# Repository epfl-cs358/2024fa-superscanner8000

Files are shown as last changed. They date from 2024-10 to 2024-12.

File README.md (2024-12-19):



# Superscanner8000
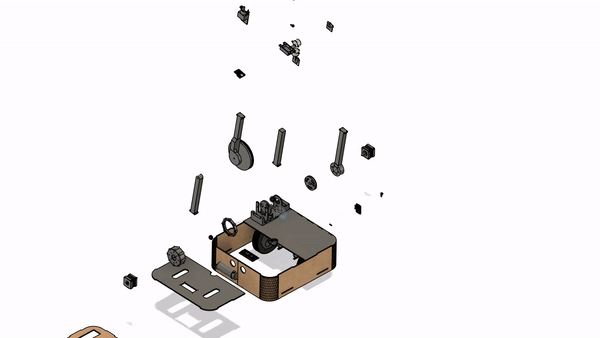
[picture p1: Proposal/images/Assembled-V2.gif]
CAD of the assembled Superrrrscanner

## Authors
   - [Noa Emien Ette](https://github.com/Noaemien)
   - [Kevan Lam Hopyang](https://github.com/KevanLam)
   - [Louis Léonard Marie Larcher](https://github.com/loulou413)
   - [Antoine Baptiste Gauthier](https://github.com/gautierantoine195)
   - [Mateo Tiedra](https://github.com/mateotiedra)
   - [Ugo Novello](https://github.com/Laggrif)

<details>
  <summary>Table of Contents</summary>
  <ol>
    <li>
      <a href="#about-the-project">About The Project</a>
      <ul>
        <li><a href="#authors">Authors</a></li>
        <li><a href="#project-description">Project Description</a></li>
        <li><a href="#project-structure">Project Structure</a></li>
      </ul>
    </li>
    <li>
      <a href="#make-your-own-superscanner8000">Make Your Own SuperScanner8000</a>
      <ul>
        <li><a href="#built-with">Built With</a></li>
        <li><a href="#prerequisites">Prerequisites</a></li>
        <li><a href="#hardware-assembly">Hardware Assembly</a></li>
        <ul>
          <li><a href="#main-body">Main Body</a></li>
          <li><a href="#arm">Arm</a></li>
          <li><a href="#gearbox">Gearbox</a></li>
          <li><a href="#motor-housings">Motor Housings</a></li>
          <li><a href="#assembly-of-the-arm">Assembly Of The Arm</a></li>
        </ul>
        <li><a href="#electronic">Electronic</a></li>
        <ul>
          <li><a href="#diagram">Diagram</a></li>
        </ul>
        <li><a href="#software">Software</a></li>
      </ul>
    </li>
    <li><a href="#gratitude-and-appreciation">Gratitude and Appreciation</a></li>
  </ol>
</details>

## Project Description 

The core of this project idea is to make a mobile robot capable of identifying the object of interest and taking pictures of it from all (possible) angles. This would be paired with a desktop application that would receive the images and apply the user-selected 3D reconstruction algorithm.

From this description, we can identify several key components the project needs:

1. **The Robot**:
   - 1.1: Navigate and plan routes around the object.
   - 1.2: Segment view and recognize the object of interest.
   - 1.3: Translate camera on the Z-axis whilst tracking the object of interest.

2. **The Desktop Application**:
   - 2.1: User can choose the object of interest.
   - 2.2: Process images sent by the robot using 3D reconstruction algorithms (NeRF, 2DGS, Multi-view stereo).

Nowadays, one does not need specialized high-end equipment to 3D scan objects. Most of us already have the necessary equipment—a smartphone, as long as it has a functioning camera and adequate software. For this project, we will not be using a smartphone, as having an integrated camera gives the robot higher usefulness without drastically increasing complexity.

In order to move the camera, we will use an arm with two segments, each powered by a stepper motor (like the Pixar lamp), fixed on top of the robot and oriented perpendicular to the wheels. In addition, the camera will be fixed to the arm using two servos offering roll and pitch control.

Most currently existing 3D object scanners are catered to small objects, rotating the object and photographing it from a fixed camera. We decided to take a different approach with the goal of providing more flexibility while keeping the complexity as low as possible.

<p align="right">(<a href="#readme-top">back to top</a>)</p>

## Project Structure

Below is a brief explanation of this repository's structure to provide context and aid readers' comprehension in the following sections of this document.
- `code` directory: contains all the code for the different parts of the project.
    - `hardware`: directory: contains all the code related to the hardware (motor movement, camera setup, connection to webserver) 
    - `software`: directory: contains all the code related to the software (webapp, navigation, reconstruction of 3d model...)
- `design` directory: contains all the 3D modeling files and exports along with the laser cut sheets.
- `diagrams` directory: contains all diagrams relate to the project
- `documentation` directory: contains all the pictures and schematics to be able to reproduce this project.
- `proposal` directory: the original document used to write the initial project proposal.

<p align="right">(<a href="#readme-top">back to top</a>)</p>

## Make your own SuperScanner8000

This section is dedicated to explaining how to build this project yourself! (All the printing/cutting part are available)

### Built with

   * [][Python-url]
   * [][Cpp-url]

### Prerequisites
Comprehensive list of elements we used in our project along with needed equipment. To construct the device, one should

Buy:

- 2 Esp-32 Cam + ov5640 (for the camera on top => better image resolution, if you got a better camera, use it)
- Lot of PETG
- 2 NEMA-17 (stepper motor) (17HS4401 + A4988)
- 2 Chihai CHF-GM37-550ABHL (brush motor) + L298N (driver)
- 2 28BYJ-48 StepperMotor (stepper motor) + ULN2003 (driver)
- QAPass 1602a

Have access to:

- LIPO Batterie
- LIPO box (you can make it your own : [LIPO Protection tuto](https://github.com/epfl-cs358/cs358-resources/tree/main/cad/lipo_protection))
- Batterie management system (3S 12V 40A Lithium Batterie BMS)
- 3D printer with TPU filament (for the outer wheel)
- 3D printer with PET filament (bunch of it, pla should make it right too)
- Laser cutting machine
- MDF board 4mm
- Airsoft Bullets (gearbox)
- 6 small ball bearings (gearbox)
- 4 small omni bearings (caster wheel)
- Ball (caster wheel : e.g. table football ball)
- 4 Magnets (QAPass)
- Belt (Arm)
- 6mm Stailness Steel bar (Arm)
- 3 mm and 2.5 mm Screws
- Driller
- Bunch of different screwdrivers
- Soldering kit

<p align="right">(<a href="#readme-top">back to top</a>)</p>

### Hardware Assembly

##### Main Body

###### Base

Laser cut the following MDF (4mm) files :
   - [Bottom Base](design/dxf/bottom_base.dxf)
   - [Side Base](design/dxf/side_full.dxf)
   - [Top Base Front](design/dxf/top_base_front.dxf)
   - [Top Base Back](design/dxf/top_base_back.dxf)
   - 3 * [Calibrate 1](design/dxf/calibrate1)
   - 3 * [Calibrate 2](design/dxf/calibrate2)

3d Print the following folder :
   - [Components Support](design/prints/components_supports)

The side is made to be foldable to give our SuperScanner8000 round corners. Be careful with these specific parts as they could break. 
You can assemble the bottom and side by glueing them but we recommend glueing the top parts once you have all the electronics setup inside.

###### Wheels

3D print the following parts : 
   - 2 * [Inner Wheel](design/prints/inner_wheel.stl)
   - 2 * [Outer Wheel](design/prints/outer_wheel.stl) (Beware you need to print this in TPU)

###### Caster Wheel

3D print the following folder : 
   - [Caster Wheel Folder](design/prints/caster)

You will also need the 4 omni bearings for this part.

###### Structures for electronics

3D print the following parts :
   - [CNC Shield Support](design/prints/CNC_shield_support.stl)
   - [ESP32-S2 Support](design/prints/ESP32-S2_support.stl)
   - [LiPo Support](design/prints/LiPo_support.stl)
   - [Chihai Support](design/prints/chihai_supports.stl)
   - [LiPo Bottom](design/prints/lipo_box/Lipo_bottom.stl)
   - [LiPo Box](design/prints/lipo_box/Lipo_box.stl)

Here, drill your own hole to make your own wire management.

##### Arm

###### Arm

3D print the parts in these folders :
   - [Arm Folder](design/prints/long_arm)
   - [Top Axle Folder](design/prints/top_axle)

3d print this part to hold the belt together :
   - [Belt Holder](design/prints/belt_holder.stl)

You should print 2 times esp_case2 for the cam in the box that we use for object detection. You will need the 6mm stainless steel bar for the elbow connection of the arm.
We opted to glue our belt into one piece instead of the belt holder in the end but both solutions are fine.

###### Gearbox

3D print the parts in the actuator folder :
   - [15th Planet Carrier](design/prints/actuators/15th_planet_carrier.stl)
   - [15th Sun](design/prints/actuators/15th_sun_stage1.stl)
   - 3 * [25th Planet Stage 1](design/prints/actuators/25th_planet_stage1.stl)
   - 3 * [25th Planet Stage 2](design/prints/actuators/25th_planet_stage2.stl)
   - [Motor Base Ring](design/prints/actuators/Nema17_base_ring.stl)
   - [Motor Clamp](design/prints/actuators/Nema17_clamp.stl)
   - [Motor Mount](design/prints/actuators/nema17_mount.stl)

You'll also need the 6 ball bearings and the airsoft bullets to create this gearbox.
We followed [this tutorial](https://www.thingiverse.com/thing:4428749/) to create our gearbox.

###### Motor Housings

3D print the following parts :
   - [Nema17 Housings](design/prints/housing_on_base.stl)

Here we also used some small carpet textile to reduce the stepper motor noise.

<p align="right">(<a href="#readme-top">back to top</a>)</p>

###### Assembly Of The Arm

Once you have printed all these components you will firstly you'll want to screw the 4 arm parts together as well as the upper arm (make sure you add the metal/stainless steel bar at the elbow and the camera in the upper arm section). You can also screw the housings to the top of the base and screw the gearbox to a stepper motor in parallel. Now you can screw the arm to the gearbox and finally place the stepper motors in the housings (first thebelt one and then the gearbox one, don't forget the carpet). Add the belt and you'll be good to go!

### Electronic
#### Diagram
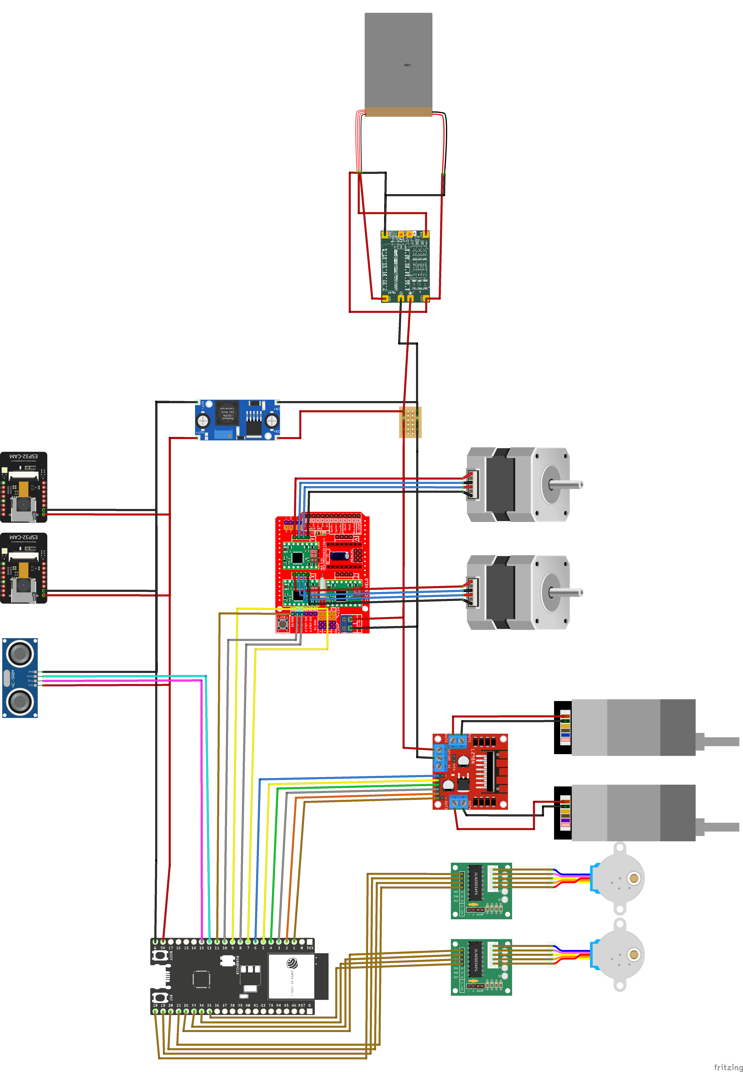
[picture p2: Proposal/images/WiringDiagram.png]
elctronic diagram


### Software
The structure of the software as well as an installation guide can be found in the [software directory](code/software).

## Possible Improvements

Here are a few improvements we thought of for this project.

### Hardware

A non-exhaustive list :
   - A better LiPo battery : ours is starting to die out and can't power the LEDs at full capacity.
   - Different / more precise motors for the wheels : our robot has slight trouble going perfectly straight.
   - A third stepper for the camera to avoid inverse kinematics.
   - Screw the elbow instead of using a stainless steel bar : would need the perfect screw that is partialy threaded so it can rotate around the other arm.
   - Metal balls for the gearbox : our airsoft balls start to melt and decompose.
   - A better design for the nema 17 housings to make sure the gear box doesn't bend due to the pull of the belt

## Gratitude and Appreciation
We would like to express our special thanks to our assisstant [Pinar](https://github.com/pinar-oray) and [Julian](https://github.com/julianmarmier), whose insights and suggestions were instrumental in shaping our super scanner. We are also grateful to [Timofey](https://github.com/kreslotim) for his technical support and encouragement and constructive feedback.

And I (Kevan) would like to thanks my peers, my friends for this fun project.

[Python.org]: https://img.shields.io/badge/Python-brightgreeen?style=flat&logo=python&logoColor=FFE873&color=306998
[Python-url]: https://www.python.org/
[Cpp.org]: https://img.shields.io/badge/C%2B%2B-blue?logo=cplusplus
[Cpp-url]: https://isocpp.org/

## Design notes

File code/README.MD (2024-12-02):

## Superscanner 8000's general structure
#### Codesource's structure
The project consists of two main directory: the software and the hardware. In the hardware directory there is all the code running in the arduino board directly attached to the robot. The software sends instructions to the hardware, and the hardware gather and share informations back to the software. In the software directory there is all the code running on the computer.

## Robot movements
The first part of the system make the robot move to the right positions around the object. To scan it as precisely as possible. In order to do that the computer and the robot are both connected to a WiFi network and the robot host a webserver on which the computer can send requests

#### Movement API
- `POST /move`: Instructs the robot to move forward. **Parameters:**
    - `direction` (string): The direction of rotation, either `forward` or `backward`.
    - `distance` (integer): The distance for which the robot should move. If it is not specified, the robot move until instructed otherwise.
- `POST /stop`: Instructs the robot to stop all movement. No parameters.
- `POST /rotate`: Instructs the robot to rotate by a specified angle. **Parameters:**
    - `direction` (string): The direction of rotation, either `left` or `right`.
    - `angle` (integer): The angle in degrees by which the robot should rotate. If it is not specified, the robot rotate until instructed otherwise.
- `POST /arm`: Instructs the robot to rotate by a specified angle. **Parameters:**
    - `hips` (integer) [0,180]: The angle in degrees between the base plan and the first segment of the arm.
    - `knee` (integer) [-180,180]: The angle difference in degrees between the first and second segment
    - `ankle` (integer) [0,360]: The angle difference in degrees between the camera to the top and the second segment

## Computing the 3D model
The robot sends the pictures it takes to the computer in order to run AI model on computer and compute the 3D model.

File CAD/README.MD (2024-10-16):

# CAD designs imported from Fusion360 team folder

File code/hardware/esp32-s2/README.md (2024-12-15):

# ESP32 API

## Overview
The API can be accessed from the `SPOT-iot` Wifi using the adress [`http://superscanner8000/`](http://superscanner8000/). The file `code/esp32-s2/esp32s2.py` makes the API available through an `ESP32S2` class for easy usage in python code.

## Endpoints

> ### GET `/status`
> return format:
> <pre><code>    {
>         "direction": one of <i>forward</i>, <i>backward</i>, <i>left</i>, <i>right</i>, <i>hard left</i>, <i>hard right</i>, <i>stop</i> 
>     }
> </code></pre>
> Returns the current movement the scanner is performing.

> ### POST `/fwd`
>    body format:
>
>        {
>            "ms": value
>        }
> 
> Makes the scanner run forward for `ms` milliseconds. If `ms <= 0` runs forever.

> ### POST `/bwd`
>    body format:
>
>        {
>            "ms": value
>        }
> 
> Makes the scanner run backward for `ms` milliseconds. If `ms <= 0` runs forever.

> ### POST `/lft`
>    body format:
>
>        {
>            "ms": value
>        }
> 
> Makes the scanner turn left for `ms` milliseconds. If `ms <= 0` runs forever.

> ### POST `/rgt`
>    body format:
>
>        {
>            "ms": value
>        }
> 
> Makes the scanner turn right for `ms` milliseconds. If `ms <= 0` runs forever.

> ### POST `/hlft`
>    body format:
>
>        {
>            "ms": value
>        }
> 
> Makes the scanner turn on itself anti-clockwise for `ms` milliseconds. If `ms <= 0` runs forever.

> ### POST `/hrgt`
>    body format:
>
>        {
>            "ms": value
>        }
> 
> Makes the scanner turn on itsels clockwise for `ms` milliseconds. If `ms <= 0` runs forever.

> ### POST `/stp`
>    
> Makes the scanner stop as quickly as possible. Does not need any body.

> ### GET `/arm/status`
>    return format:
>
>        {
>            "x": x position where the arm is
>            "y": y position where the arm is
>            "q1": angle of first stepper in degrees
>            "q2": angle of the second stepper in degrees
>            "moving": boolean indicating whether the arm is moving or not
>        }
> 
> Returns informations about the arm.

> ### POST `/arm/goto`
>    body format:
>
>        {
>            "x": target x position
>            "y": target y position
>            "angles": boolean indicationg whether x and y are positions or angles
>        }
> 
> Makes the arm move to the given position
>> might return error code `422` if coordinates or angles are not valid

> ### POST `/arm/stop`
> 
> Stops the arm as quickly as possible. Does not need any body

> ### GET `/cam/status`
>    return format:
>
>        {
>            "alpha": alpha angle where the cam wants to go
>            "beta": beta angle where the cam wants to go
>            "moving": boolean indicating whether the camera is moving or not
>        }
> 
> Returns informations about the camera.

> ### POST `/cam/goto`
>    body format:
>
>        {
>            "alpha": target angle for vertical movement
>            "betha": target angle for horizontal movement
>        }
> 
> Makes the camera move to the given angles
>> Might return error code `422` if angles are not valid

> ### POST `/cam/stop`
> 
> Stops the camera as quickly as possible. Does not need any body

## class `ESP32S2`

Interfaces with the API to provide an abstracted access to the scanner.

> ### `ESP32S2()`
> Class constructor. Does not require any parameters.

> ### `forward(self, time)`
> - `time`: duration of movement in ms. Moves infinitely if <= 0
> - returns: `0` if operation was successful, `-1` otherwise

> ### `backward(self, time)`
> - `time`: duration of movement in ms. Moves infinitely if <= 0
> - returns: `0` if operation was successful, `-1` otherwise

> ### `left(self, time)`
> - `time`: duration of movement in ms. Moves infinitely if <= 0
> - returns: `0` if operation was successful, `-1` otherwise

> ### `right(self, time)`
> - `time`: duration of movement in ms. Moves infinitely if <= 0
> - returns: `0` if operation was successful, `-1` otherwise

> ### `hard_left(self, time)`
> - `time`: duration of movement in ms. Moves infinitely if <= 0
> - returns: `0` if operation was successful, `-1` otherwise

> ### `hard_right(self, time)`
> - `time`: duration of movement in ms. Moves infinitely if <= 0
> - returns: `0` if operation was successful, `-1` otherwise

> ### `stop(self)`
> - returns: `0` if operation was successful, `-1` otherwise

> ### `direction(self)`
> - returns: a `string` giving the current direction or `None` if request was unsuccessful

> ### `arm.goto(self, x_coord, y_coord)`
> - `x_coord`: target x coordinate in cm
> - `y_coord`: target y coordinate in cm
> - returns: `0` if operation was successful, `-1` otherwise

> ### `arm.stop(self)`
> - returns: `0` if operation was successful, `-1` otherwise

> ### `arm.pos(self)`
> - returns: `(x, y)` tuple representing the target coordinated of the arm or `None` if the request was unsuccessful

> ### `arm.is_moving(self)`
> - returns: a `boolean` indicating whether the arm is moving or `None` if the request was unsuccessful

## `__main__` in `esp32s2.py`

Running `esp32s2.py` provides a small graphical interface to test movements without having to write code.

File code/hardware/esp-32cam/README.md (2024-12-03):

Run the Esp32-cam.ino on the esp and then run the socket receiver.py The python script will send the computer's IP and the Esp will use this ip to create an udp connection and send the frames it captures.

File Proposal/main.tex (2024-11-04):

\documentclass{article}
\usepackage[utf8]{inputenc}
\usepackage{textcomp}
\usepackage{gensymb}
\usepackage{geometry}
\usepackage{fancyhdr}
\usepackage{tkz-euclide}
\usepackage{ragged2e}
\usepackage{hyperref}
\usepackage{float}
\usepackage{tikz}
\usepackage{float}
\usepackage{multirow}
\usepackage{biblatex}
\usepackage[graphicx]{realboxes}
\addbibresource{refs.bib}

\pagestyle{fancy}
\geometry{top=3cm, bottom=2.5cm, left=3.5cm, right=3.5cm}
\rhead{CS-358}
\lhead{\leftmark}
\fancyfoot[R]{\leftmark}
\fancyfoot[C]{}
\fancyfoot[L]{Page \thepage}
\renewcommand{\footrulewidth}{1pt}
\usepackage{multicol}
\title{CS-358: Individual Project Proposal}
\author{Noa Ette - 363760\\Mateo Tiedra - 356525\\Kevan Lam - 356395\\Louis Larcher - 361002\\Ugo Novello - 329763\\Antoine Gautier - 356442}
\date{\today}

\begin{document}

\maketitle
\vspace{45mm}
\tableofcontents
\newpage
\section{Project Description: Autonomous 3d Object Scanner}

The core of this project idea is to make a mobile robot capable of identifying the object of interest and taking pictures of it from all (possible) angles. 
This would be paired with a desktop application that would receive the images and apply the user selected 3d reconstruction algorithm.\\

From this description we can identify several key components the project needs: \begin{enumerate}
    \item \texttt{The Robot}:
    \begin{description}
            \item[1.1] Navigate and plan routes around object.
            \item[1.2] Segment view and recognize object of interest.
            \item[1.3] Translate camera on z axis whilst tracking object of interest.
    \end{description}
    \item \texttt{The Desktop Application}:
    \begin{description}
        \item[2.1] User can choose object of interest.
        \item[2.2] Process images sent by robot using 3d reconstruction algorithms (NeRF \cite{mildenhall2020nerf}, 2DGS \cite{Huang2DGS2024}, Multi-view stereo)
    \end{description}
\end{enumerate}

Nowadays, one does not need specialised high end equipment in order to 3d scan objects. Most of us already have the sufficient equipment needed, a smartphone, given that it has a functioning camera and the adequate software. \\
For this project we will not be using a smartphone as it gives the robot higher usefulness and does not drastically increase complexity to have an integrated camera. 

In order to move the camera we will use an arm with two segments each powered by a stepper motor (like the Pixar lamp) fixed on top of the robot and oriented perpendicular to the wheels. In addition, the camera will be fixed to the arm using two servos offering roll and pitch control.

Most currently existing 3d Object scanners are catered to small objects \cite{desktop3dscanner}, rotating the object and photographing it from a fixed camera. We decided to take a different approach with the goal to give more flexibility while keeping the complexity as low as possible.

\newpage
\section{Related Projects}
We have looked at various related projects whilst trying to figure out how to design ours in the best possible manner.

We figured a mostly square base with two motors placed on diagonal wheels would be the most practical while being resource efficient and simple. This setup allows the "car" part of the robot to spin on itself, removing the need of having the arm holding the camera spin. This kind of movement is principally inspired by tanks, excavators and other tracked vehicles, except the two wheels on each side are independent instead of linked by a track.

The arm on the other hand takes inspiration from the many existing robotic or industrial arms existing. More particularly, we found this design \cite{cameraArm} which achieves a similar purpose as ours. Moving the motor for the second joint to the base is a key element of the design since it allows to have weaker motors and an overall lower center of gravity.

Unfortunately we have been unsuccessful in finding a project where a robot tracks an object, rotating around it. This poses a particular computer vision challenge as the robot needs to be able to recognise the object from completely distinct angles. Thanks to the fact that the robot will be navigating using video from an ESP32-CAM on the front of the robot, basic object tracking like those in opencv will most likely be sufficient.

\section{User Stories}

The final product of this project is something that could be useful to many people from different horizons. \\
In one case, one could imagine a real estate agent, wanting to provide virtual visits of a home he is selling. Instead of having to contact a freelance 3D artist to remodel the home, probably costing thousands, they would be able to simply 3d scan the area using the robot and software made in this project, saving plenty of time and money. Some companies have already ventured into real-estate specific 3d scanning \cite{matterport}. \\
Another imaginable use case is for professional 3d artists wanting to use realistic large objects in their 3d scenes. The conventional way to scan these objects would be to manually take pictures of them. Something that is very time consuming and sometimes requires particular gymnastics skills.
I personally have a little bit of experience with manually 3d scanning objects and can personally attest that, depending on the object, it can take a frustratingly long amount of time.

It could be an interesting demonstration for the EPFL Open House as it demonstrates the link between 3d art and computer science by leveraging an intelligent robot to optimise the workload of different career paths.

\section{Long term view}

Given a long term viewpoint, we could easily imagine different form factors being based on this project being developed for many different use cases. 

At a much larger scale, terrestrial and aerial 3d scanning robots could be used to map entire city's. Re-creating what would take thousands if not millions of man hours. This data could be used to train autonomous vehicles on real city's though simulation or for many other projects.

At a smaller scale, this technology could be redesigned on an aquatic form factor in order to map ocean floors and areas inaccessible by humans.

\newpage
\section{Physical description}

The robot takes the form of a square "car" with four wheels, 2 of which are powered by brushed motors. An ESP-32 cam on the front of the car allows to make decisions on the movement of the car regarding it environment, this will be further detailed in the next section. On top of the car lies an arm with two joints, each powered by a stepper motor. The arm is facing perpendicular to the direction of travel and on top of it is mounted a second esp-32 cam with an upgraded OV5640 camera. This camera contributes to the navigation but most importantly takes pictures of the object of interest from different angles and at different heights for later reconstruction. The camera is fixed to the arm using two servos, one controlling the pitch and the other the roll.

Regarding the control of all these motors, both esp-32 cam being quite limited in terms of I/O, we have a third micro-controller to handle them.

In terms of power, our thing will work on LiPo batteries, with a battery management board and voltage converters ensuring adequate power to all parts.

See images in the next page for a visual representation of the robot.

\newpage

\begin{figure}[H]
    \centering
    \begin{minipage}{0.45\textwidth}
        \centering
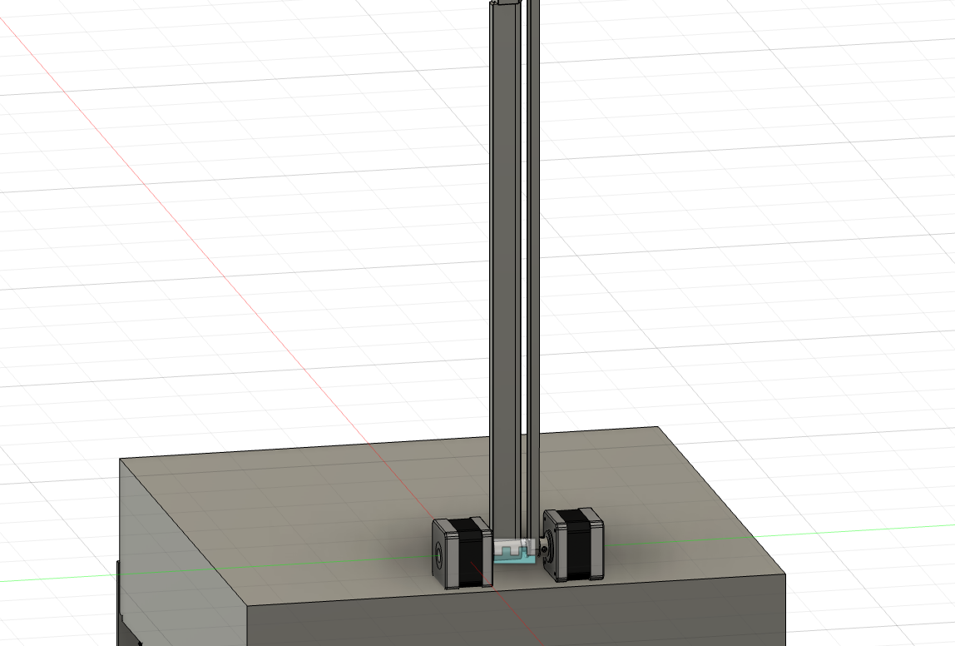
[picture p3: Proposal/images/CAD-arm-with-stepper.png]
        
        \caption{Arm with stepper motors}
        \label{fig:image1}
    \end{minipage}
    \hfill
    \begin{minipage}{0.45\textwidth}
        \centering
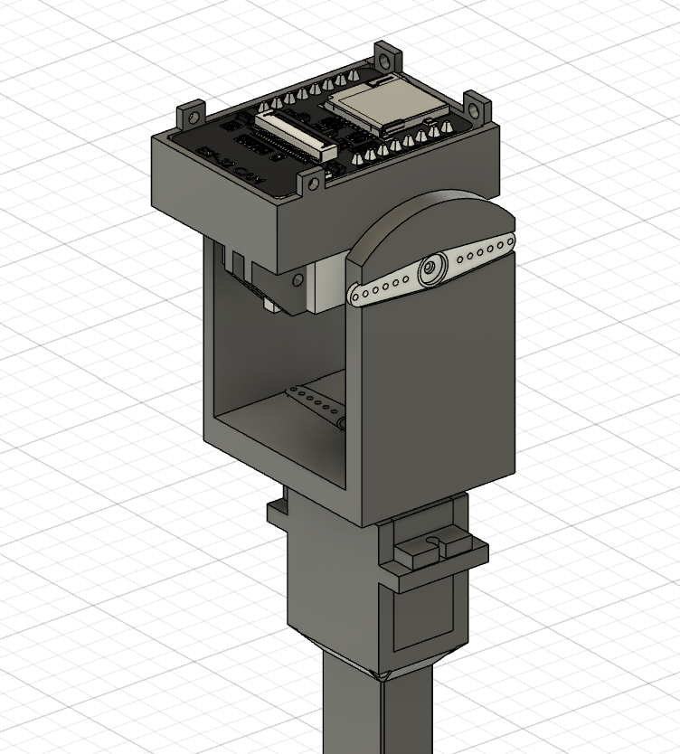
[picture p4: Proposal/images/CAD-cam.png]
        
        \caption{Head of the arm with camera}
        \label{fig:image2}
    \end{minipage}
    \label{fig:sidebyside}
\end{figure}

\begin{figure}[H]
    \centering
    \begin{minipage}{0.45\textwidth}
        \centering
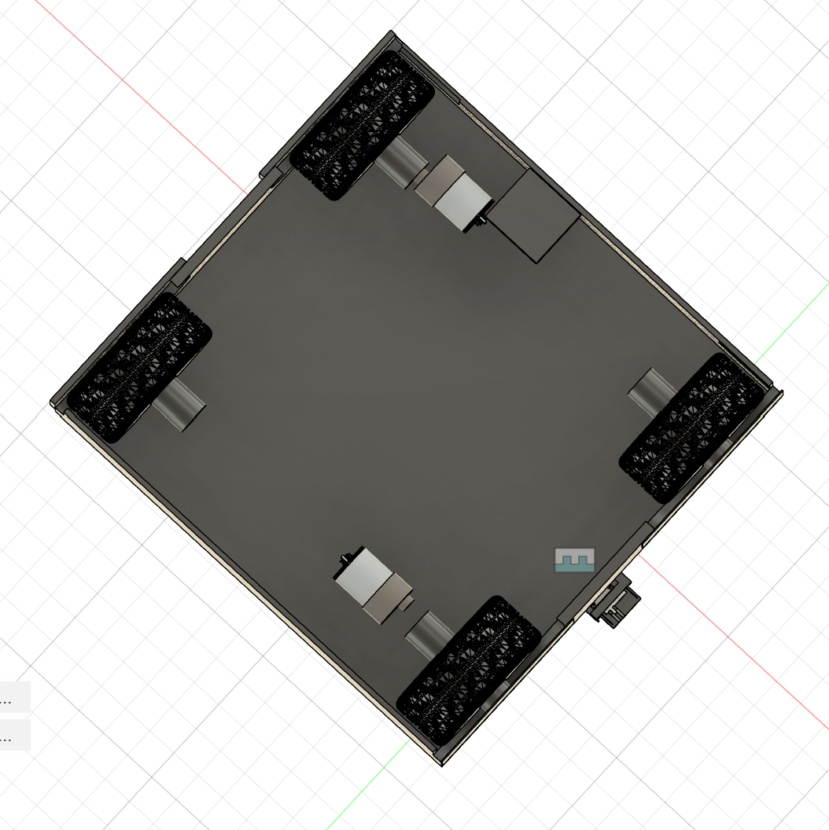
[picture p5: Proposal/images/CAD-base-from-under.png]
        
        \caption{Base and wheels from underneath}
        \label{fig:image1}
    \end{minipage}
    \hfill
    \begin{minipage}{0.45\textwidth}
        \centering
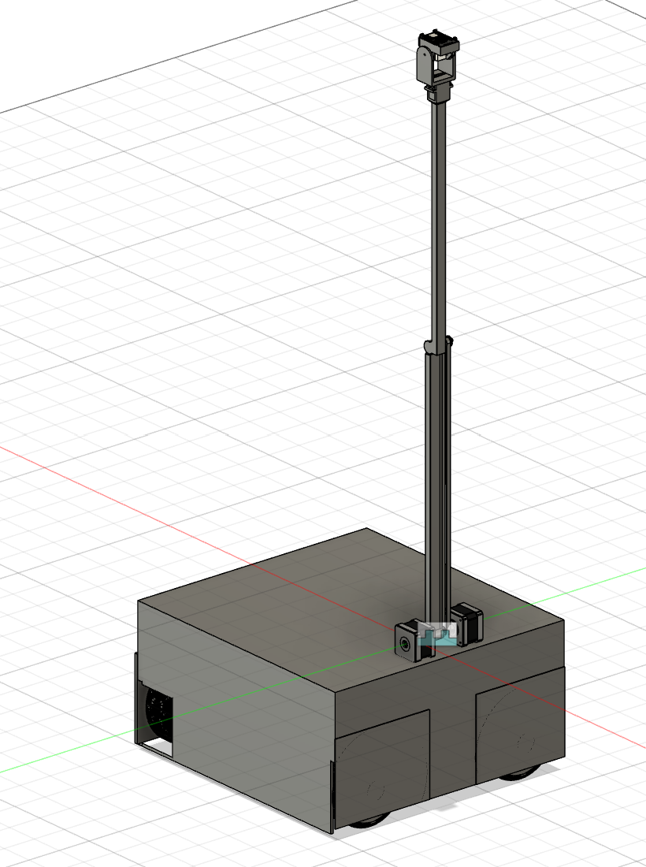
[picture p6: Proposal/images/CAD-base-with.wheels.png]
        
        \caption{Full robot with wheels}
        \label{fig:image2}
    \end{minipage}
    \label{fig:sidebyside}
\end{figure}

\newpage

\section{Software description}

The Superscanner8000 software run on a computer connected to the robot through Wi-Fi. The program allows users to select an object within the camera’s field of view and adjust a parameter that specifies the level of precision needed, determining the number of photos the robot will capture. Once selected, the software guides the robot to navigate around the object, capturing images from various angles and distances. After gathering a sufficient number of images, the software processes them to generate a 3D model of the object, which can then be exported.

To enable the user to select an object for scanning, the software displays the live video feed from the robot camera on the screen, showing various objects in view. The user can click directly on the object of interest, which will then be detected and highlighted using Meta's open-source model, SAM 2.

\begin{figure}[H]
    \centering
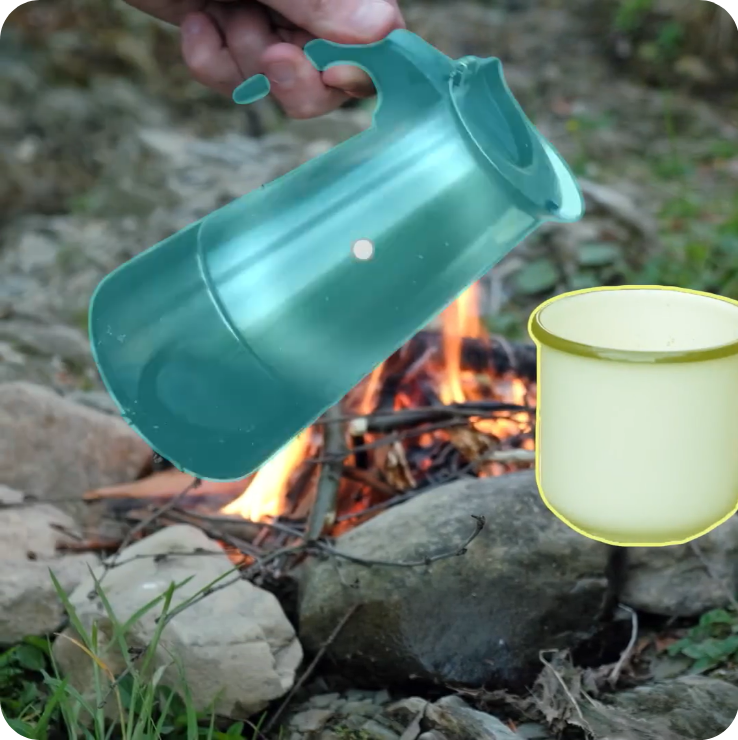
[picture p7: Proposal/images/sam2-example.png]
    
    \caption{Example of SAM 2's image segmentation}
    \label{fig:sam2-example}
\end{figure}

After the object is selected, the software directs the robot to move in a circular path around it. The robot moves in one direction while simultaneously using object segmentation to keep the object centered in the camera's field of view, rotating its entire body to maintain this alignment. Once it has completed a portion of the path, the software halts the robot, allowing it to capture images from different angles by adjusting the arm and raising or lowering the camera and the starts it again to move to the next position. This process is repeated until the robot has completed a full circle around the object. The user can stop the process at any time with a button on the software interface.

The images are transmitted from the robot to the computer in real time as the device moves and captures additional photos. Once the robot completes its data-gathering walk around the object and all images have been uploaded to the computer, the system initiates the 3D object conversion process using 3D reconstruction algorithms such as 2DGS \cite{Huang2DGS2024} and NeRF \cite{mildenhall2020nerf}.

\newpage
\section{Wiring diagram}
\begin{figure}[H]
    \centering
    
    \caption{Wiring diagram (parts not to scale)}
    \label{fig:wiring-diagram}
\end{figure}

\newpage
\section{Bill of materials}

\begin{center}
\Rotatebox{90}{%
\begin{tabular}{ ||c|c|c|c|c|c|| } 

\hline
Category & Type & Name & Site & Amount & Price \\
\hline
\hline
\multirow{4}{5em}{Actuators} 
& brushed motor & Chihai CHF-GM37-550ABHL & [In stock] & 2 & 25 \\ 
& brushed driver & L298N & [In stock] & 2 & 5\\
& stepper + driver & 17HS4401 + A4988 & [In stock] & 2 & 15 \\
& servo & SG90 & [In stock] & 2 & 3 \\
\hline
\hline
\multirow{4}{5em}{Controllers} 
& controller + camera & AIThinker esp32-cam & [In stock] & 2 & 4\\ 
& camera & OV5640 & \href{https://www.digikey.ch/fr/products/detail/seeed-technology-co-ltd/114993115/21277047}{digikey.ch} & 1 & 10.89\\ 
& microcontroller & ESP32-S2-DEVKITM-1U-N4R2 & \href{https://www.digikey.ch/fr/products/detail/espressif-systems/ESP32-S2-DEVKITM-1U-N4R2/16688756}{digikey.ch} & 1 & 7.27\\
& UART to USB & FTDI USB-to-serial & [In stock] & 1 & 2\\
\hline
\hline
\multirow{1}{5em}{Sensors}
& ultrasonic sensor & HC-SR04 & [In stock] & 1 & 2\\
\hline
\hline
\multirow{8}{5em}{Power}
& battery & Absima 11.1 V 6000 mAh 3S 50 C & \href{https://www.conrad.ch/fr/p/absima-pack-de-batterie-lipo-11-1-v-6000-mah-nombre-de-cellules-3-50-c-stick-xt90-3322657.html}{conrad.ch} & 1 & 51.95 \\
& BMS & 3S 12V 40A BMS & \href{https://www.elektronik-kaufen.ch/products/bms-3s-40a?variant=41643639701680&currency=CHF}{elektronik-kaufen.ch} & 1 & 5.5 \\
& heatsink & aluminum sheet & [In SPOT shop] & 1 & 10 \\
& battery plug male & XT90-S male plug & \href{https://www.conrad.ch/fr/p/reely-re-6702312-fiche-male-pour-batterie-xt90-s-dore-e-1-pc-s-2234104.html}{conrad.ch} & 2 & 1.9 \\
& battery plug female & XT90-S female plug & \href{https://www.conrad.ch/fr/p/reely-re-7471836-prise-femelle-pour-batterie-xt90-dore-e-1-pc-s-2490612.html}{conrad.ch} & 1 & 1.6 \\
& load balance plug & JST XH2.54 3p 20cm & \href{https://www.bastelgarage.ch/cable-de-connexion-jst-xh2-54-3p-20cm}{bastelgarage.ch} & 1 & 0.6 \\
& dc power plug & DC Socket Female Barrel Jack 5.5mm / 2.1mm & \href{https://www.bastelgarage.ch/dc-socket-female-barrel-jack-5-5mm-2-1mm-with-screw-terminals?search=dc%20female}{bastelgarage.ch} & 1 & 1.9\\
& voltage converter & LM2596 & [In stock] & 2 & 3 \\
\hline
\hline
\multicolumn{5}{|r|}{total cost} & 203.61\\
\hline
\hline
\end{tabular}
}%
\end{center}

\newpage

\section{Risk Assessment}

Here we will talk about potential risks for the success of the SuperScanner8000 project. Let’s start by focusing on the difficulties linked to the hardware. 

A basic concern is the voltage supply. We have decided to use a LIPO battery to supply our robot. This decision was made after making calculations and verifying that this battery would be enough for all our motors, drivers and microcontrollers. As shown in the bill of materials we also made sure to include all the extra components needed to accompany our LIPO battery. Of course, we will still have to make diagrams for all the electronics before plugging everything in to make sure it all works as planned.

Another typical concern is the power of our actuators. We have also run calculations for our wheels and our arm to make sure the brush/stepper motors were powerful enough. The servos for the camera should also be a good fit however we might have to adapt if we end up using a phone as our camera. All of this will of course have to be retested once we print out the pieces as shown in the GANTT chart.

Speaking of cameras, we also had a tough time finding the appropriate camera for this project. In the end we are choosing to go for the OV5640 camera which should have sufficient quality for recognition and reconstruction of 3d objects. We have thought of alternatives in case of this camera not working out for us, notably using a phone camera.

One last hardware concern is the stability of our SuperScanner8000. The arm should be able to move everywhere without throwing the robot out of balance. We have made multiple design choices like having the arm be orthogonal to the wheels or using a belt for the arm to attempt to reduce this problem however we will once again have to test this once we print the materials and assemble the robot.

Now moving onto the software side. 
One crucial concern is the one of communication between multiple microcontrollers. Our SuperScanner8000 will possess more than one microcontroller as the esp-32 driver does not have enough pins for all our motors. This means that we will have to make sure early on we can make our microcontrollers speak to each other. Notably here we want our camera to take a picture and then move around the object while also communicating to the other camera to make sure we don’t run into any obstacles. Thankfully all our microcontrollers are equipped with Wi-Fi which should let them communicate at a rapid speed.

This also leads us to our second concern which is the communication to the computer who is running the app. We will have to send photos taken by the cameras, compute our next move and send that information back. This will also have to be done through Wi-Fi and will have to be explored early on.

A very important problem we have to tackle in this project is the very basis of it : scanning 3d objects. Our team will have to code a program that is able to use the photos communicated by the robot to recognise and recreate accurate depictions of the 3d object. A lot of libraries and tools already exist for 3d scanning which will be of great help for us. We will also have to make sure we move around the object close enough so that we can recreate a good 3d model of high quality everywhere. This also means taking pictures of the underneath of a table for example which means we should be confident enough to guide our robot all around the 3d object. Optionally we also want to tackle the case of room scanning which involves the robot being capable of moving everywhere inside a room. It is possible we are being too optimistic about 3d scanning, that is why we have set some of the tasks as optional. This leaves us the freedom to spend more time on the basis of the project but also opens possibilities if we find time. Thankfully we have someone who knows a lot about 3d scanning : Noa Ette. He has already worked on such projects and feels confident that as a team we can succeed. With his guidance, the rest of the team should be able to learn more quickly about recognition and reconstruction basics.

Another closely linked problem is the obstacle avoidance issue. We will need this obstacle avoidance if we want to scan an object while others are around it or if we want to do the room scanning. Once again this is an optional task but it is important to state now what could potentially go wrong with it. The issue here will once again be to translate 2d images into something the SuperScanner8000 can understand and prepare against. Once again online libraries will be our biggest allies here and we will have to learn how to use them.

\newpage

\section{GANTT Chart}

\begin{figure}[H]
    \centering
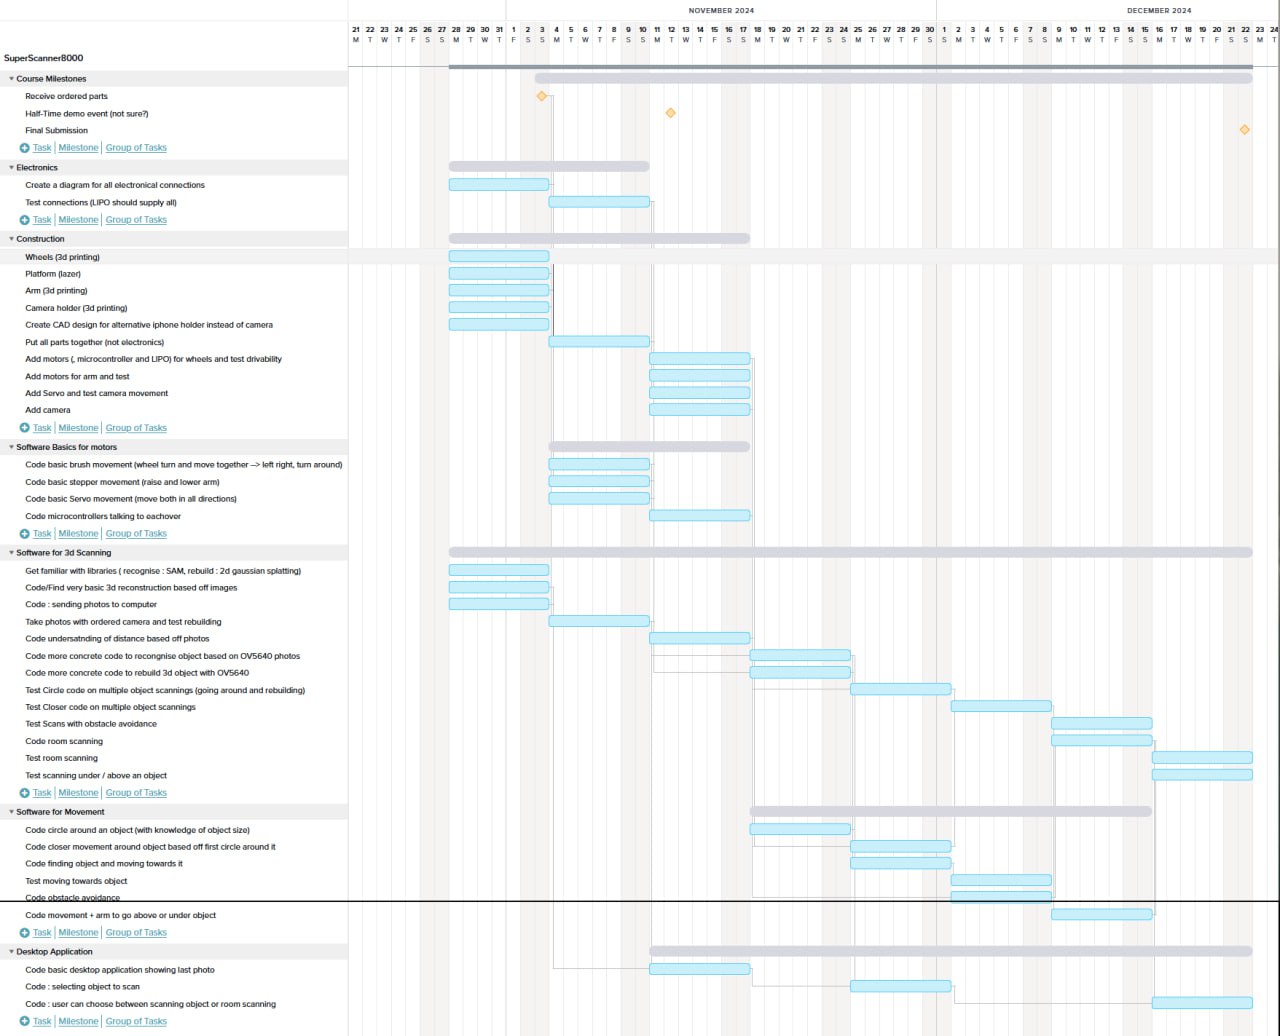
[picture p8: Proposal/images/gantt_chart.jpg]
    \rotatebox{90}{}
    \caption{Sceenshot of GANTT Chart made on teamgantt}
    \label{fig:gantt_chart}
\end{figure}

(Apologies for the bad quality, we couldn't export from teamgantt without using the pay option)

\newpage

\printbibliography

\end{document}

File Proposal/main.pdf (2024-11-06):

# CS-358: Individual Project Proposal

Noa Ette - 363760
Mateo Tiedra - 356525
Kevan Lam - 356395
Louis Larcher - 361002
Ugo Novello - 329763
Antoine Gautier - 356442

November 6, 2024

## Contents

1 Project Description: Autonomous 3d Object Scanner | 2
2 Related Projects | 3
3 User Stories | 3
4 Long term view | 3
5 Physical description | 4
6 Software description | 6
7 Wiring diagram | 7
8 Bill of materials | 8
9 Risk Assessment | 9
10 GANTT Chart | 11

1

1 PROJECT DESCRIPTION: AUTONOMOUS 3D OBJECT SCANNER | CS-358

## 1 Project Description: Autonomous 3d Object Scanner

The core of this project idea is to make a mobile robot capable of identifying the object of interest and taking pictures of it from all (possible) angles. This would be paired with a desktop application that would receive the images and apply the user selected 3d reconstruction algo-rithm.

From this description we can identify several key components the project needs:

1. The Robot:

1.1 Navigate and plan routes around object.

1.2 Segment view and recognize object of interest.

1.3 Translate camera on z axis whilst tracking object of interest.

2. The Desktop Application:

2.1 User can choose object of interest.

### 2.2 Process images sent by robot using 3d reconstruction algorithms (NeRF [3], 2DGS

[2], Multi-view stereo)

Nowadays, one does not need specialised high end equipment in order to 3d scan objects. Most of us already have the sufficient equipment needed, a smartphone, given that it has a functioning camera and the adequate software.
For this project we will not be using a smartphone as it gives the robot higher usefulness and does not drastically increase complexity to have an integrated camera.
In order to move the camera we will use an arm with two segments each powered by a stepper motor (like the Pixar lamp) fixed on top of the robot and oriented perpendicular to the wheels. In addition, the camera will be fixed to the arm using two servos offering roll and pitch control. Most currently existing 3d Object scanners are catered to small objects [5], rotating the object and photographing it from a fixed camera. We decided to take a different approach with the goal to give more flexibility while keeping the complexity as low as possible.
Page 2 | 1 PROJECT DESCRIPTION: AUTONOMOUS 3D OBJECT SCANNER

4 LONG TERM VIEW | CS-358

## 2 Related Projects

We have looked at various related projects whilst trying to figure out how to design ours in the best possible manner.
We figured a mostly square base with two motors placed on diagonal wheels would be the most practical while being resource efficient and simple. This setup allows the ”car” part of the robot to spin on itself, removing the need of having the arm holding the camera spin. This kind of movement is principally inspired by tanks, excavators and other tracked vehicles, except the two wheels on each side are independent instead of linked by a track.
The arm on the other hand takes inspiration from the many existing robotic or industrial arms existing. More particularly, we found this design [4] which achieves a similar purpose as ours. Moving the motor for the second joint to the base is a key element of the design since it allows to have weaker motors and an overall lower center of gravity.
Unfortunately we have been unsuccessful in finding a project where a robot tracks an object, rotating around it. This poses a particular computer vision challenge as the robot needs to be able to recognise the object from completely distinct angles. Thanks to the fact that the robot will be navigating using video from an ESP32-CAM on the front of the robot, basic object tracking like those in opencv will most likely be sufficient.

## 3 User Stories

The final product of this project is something that could be useful to many people from different horizons.
In one case, one could imagine a real estate agent, wanting to provide virtual visits of a home he is selling. Instead of having to contact a freelance 3D artist to remodel the home, probably costing thousands, they would be able to simply 3d scan the area using the robot and software made in this project, saving plenty of time and money. Some companies have already ventured into real-estate specific 3d scanning [1].
Another imaginable use case is for professional 3d artists wanting to use realistic large objects in their 3d scenes. The conventional way to scan these objects would be to manually take pictures of them. Something that is very time consuming and sometimes requires particular gymnastics skills. I personally have a little bit of experience with manually 3d scanning objects and can personally attest that, depending on the object, it can take a frustratingly long amount of time. It could be an interesting demonstration for the EPFL Open House as it demonstrates the link between 3d art and computer science by leveraging an intelligent robot to optimise the workload of different career paths.

## 4 Long term view

Given a long term viewpoint, we could easily imagine different form factors being based on this project being developed for many different use cases.
At a much larger scale, terrestrial and aerial 3d scanning robots could be used to map entire city’s. Re-creating what would take thousands if not millions of man hours. This data could be used to train autonomous vehicles on real city’s though simulation or for many other projects. At a smaller scale, this technology could be redesigned on an aquatic form factor in order to map ocean floors and areas inaccessible by humans.
Page 3 | 4 LONG TERM VIEW

5 PHYSICAL DESCRIPTION | CS-358

## 5 Physical description

The robot takes the form of a square ”car” with four wheels, 2 of which are powered by brushed motors. An ESP-32 cam on the front of the car allows to make decisions on the movement of the car regarding it environment, this will be further detailed in the next section. On top of the car lies an arm with two joints, each powered by a stepper motor. The arm is facing perpendicular to the direction of travel and on top of it is mounted a second esp-32 cam with an upgraded OV5640 camera. This camera contributes to the navigation but most importantly takes pictures of the object of interest from different angles and at different heights for later reconstruction. The camera is fixed to the arm using two servos, one controlling the pitch and the other the roll.
Regarding the control of all these motors, both esp-32 cam being quite limited in terms of I/O, we have a third micro-controller to handle them.
In terms of power, our thing will work on LiPo batteries, with a battery management board and voltage converters ensuring adequate power to all parts.
See images in the next page for a visual representation of the robot.
Page 4 | 5 PHYSICAL DESCRIPTION

5 PHYSICAL DESCRIPTION | CS-358


Figure 1: Arm with stepper motors


Figure 2: Head of the arm with camera


Figure 3: Base and wheels from underneath


Figure 4: Full robot with wheels

Page 5 | 5 PHYSICAL DESCRIPTION

6 SOFTWARE DESCRIPTION | CS-358

## 6 Software description

The Superscanner8000 software run on a computer connected to the robot through Wi-Fi. The program allows users to select an object within the camera’s field of view and adjust a parameter that specifies the level of precision needed, determining the number of photos the robot will capture. Once selected, the software guides the robot to navigate around the object, capturing images from various angles and distances. After gathering a sufficient number of images, the software processes them to generate a 3D model of the object, which can then be exported. To enable the user to select an object for scanning, the software displays the live video feed from the robot camera on the screen, showing various objects in view. The user can click directly on the object of interest, which will then be detected and highlighted using Meta’s open-source model, SAM 2.


Figure 5: Example of SAM 2’s image segmentation

After the object is selected, the software directs the robot to move in a circular path around it. The robot moves in one direction while simultaneously using object segmentation to keep the object centered in the camera’s field of view, rotating its entire body to maintain this alignment. Once it has completed a portion of the path, the software halts the robot, allowing it to capture images from different angles by adjusting the arm and raising or lowering the camera and the starts it again to move to the next position. This process is repeated until the robot has completed a full circle around the object. The user can stop the process at any time with a button on the software interface.
The images are transmitted from the robot to the computer in real time as the device moves and captures additional photos. Once the robot completes its data-gathering walk around the object and all images have been uploaded to the computer, the system initiates the 3D object conversion process using 3D reconstruction algorithms such as 2DGS [2] and NeRF [3].
Page 6 | 6 SOFTWARE DESCRIPTION

7 WIRING DIAGRAM | CS-358

## 7 Wiring diagram

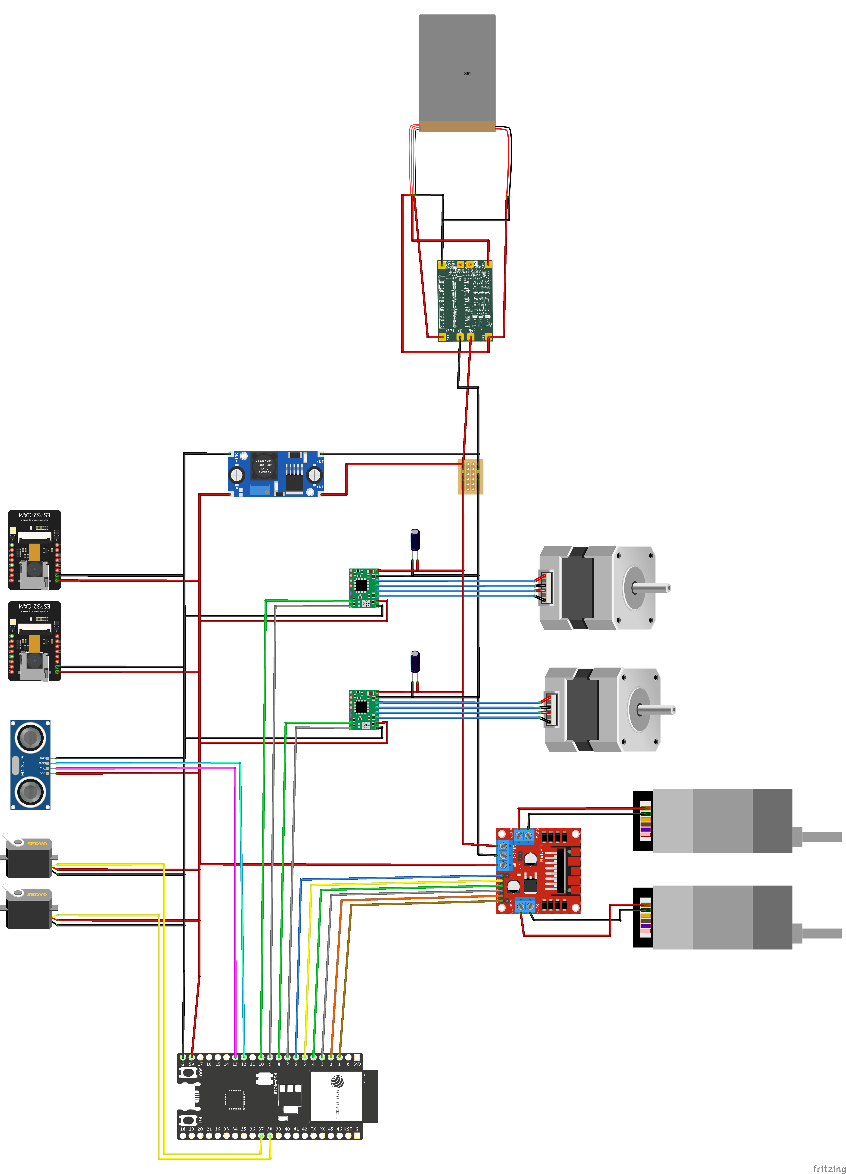
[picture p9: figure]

Figure 6: Wiring diagram (parts not to scale)

Page 7 | 7 WIRING DIAGRAM

8 BILL OF MATERIALS | CS-358
8 | Bill of materials Category Type Name Site Amount Price | Actuators brushed motor Chihai CHF⁻GM³⁷⁻⁵⁵⁰ABHL [In stock] 2 25 brushed driver L²⁹⁸N [In stock] 2 5 stepper + driver 17HS4401 + A⁴⁹⁸⁸ [In stock] 2 15

servo SG90 [In stock] 2 3

Controllers

controller + camera AIThinker esp32-cam [In stock] 2 4

camera OV5640 digikey.ch 1 10.89
microcontroller ESP32-S2-DEVKITM-1U-N4R2 digikey.ch 1 7.27
UART to USB FTDI USB-to-serial [In stock] 1 2

Sensors ultrasonic sensor HC-SR04 [In stock] 1 2

Power

battery Absima 11.1 V 6000 mAh 3S 50 C conrad.ch 1 51.95
BMS 3S 12V 40A BMS elektronik-kaufen.ch 1 5.5
heatsink aluminum sheet [In SPOT shop] 1 10

battery plug male XT90-S male plug conrad.ch 2 1.9

battery plug female XT90-S female plug conrad.ch 1 1.6

load balance plug JST XH2.54 3p 20cm bastelgarage.ch 1 0.6

dc power plug DC Socket Female Barrel Jack 5.5mm / 2.1mm bastelgarage.ch 1 1.9
voltage converter LM2596 [In stock] 2 3

total cost 203.61

Page 8 | 8 BILL OF MATERIALS

9 RISK ASSESSMENT | CS-358

## 9 Risk Assessment

Here we will talk about potential risks for the success of the SuperScanner8000 project. Let’s start by focusing on the difficulties linked to the hardware.
A basic concern is the voltage supply. We have decided to use a LIPO battery to supply our robot. This decision was made after making calculations and verifying that this battery would be enough for all our motors, drivers and microcontrollers. As shown in the bill of materials we also made sure to include all the extra components needed to accompany our LIPO battery. Of course, we will still have to make diagrams for all the electronics before plugging everything in to make sure it all works as planned.
Another typical concern is the power of our actuators. We have also run calculations for our wheels and our arm to make sure the brush/stepper motors were powerful enough. The servos for the camera should also be a good fit however we might have to adapt if we end up using a phone as our camera. All of this will of course have to be retested once we print out the pieces as shown in the GANTT chart.
Speaking of cameras, we also had a tough time finding the appropriate camera for this project. In the end we are choosing to go for the OV5640 camera which should have sufficient quality for recognition and reconstruction of 3d objects. We have thought of alternatives in case of this camera not working out for us, notably using a phone camera.
One last hardware concern is the stability of our SuperScanner8000. The arm should be able to move everywhere without throwing the robot out of balance. We have made multiple design choices like having the arm be orthogonal to the wheels or using a belt for the arm to attempt to reduce this problem however we will once again have to test this once we print the materials and assemble the robot.
Now moving onto the software side. One crucial concern is the one of communication between multiple microcontrollers. Our SuperScanner8000 will possess more than one microcontroller as the esp-32 driver does not have enough pins for all our motors. This means that we will have to make sure early on we can make our microcontrollers speak to each other. Notably here we want our camera to take a picture and then move around the object while also communicating to the other camera to make sure we don’t run into any obstacles. Thankfully all our microcontrollers are equipped with Wi-Fi which should let them communicate at a rapid speed.
This also leads us to our second concern which is the communication to the computer who is running the app. We will have to send photos taken by the cameras, compute our next move and send that information back. This will also have to be done through Wi-Fi and will have to be explored early on.
A very important problem we have to tackle in this project is the very basis of it : scanning 3d objects. Our team will have to code a program that is able to use the photos communicated by the robot to recognise and recreate accurate depictions of the 3d object. A lot of libraries and tools already exist for 3d scanning which will be of great help for us. We will also have to make sure we move around the object close enough so that we can recreate a good 3d model of high quality everywhere. This also means taking pictures of the underneath of a table for example which means we should be confident enough to guide our robot all around the 3d object. Optionally we also want to tackle the case of room scanning which involves the robot being capable of moving everywhere inside a room. It is possible we are being too optimistic about 3d scanning, that is why we have set some of the tasks as optional. This leaves us the freedom to spend more time on the basis of the project but also opens possibilities if we find time. Thankfully we have someone who knows a lot about 3d scanning : Noa Ette. He has already worked on such projects and feels confident that as a team we can succeed. With his guidance, the rest of the team should be able to learn more quickly about recognition and reconstruction basics.
Another closely linked problem is the obstacle avoidance issue. We will need this obstacle avoidance if we want to scan an object while others are around it or if we want to do the room scanning. Once again this is an optional task but it is important to state now what
Page 9 | 9 RISK ASSESSMENT

9 RISK ASSESSMENT | CS-358

could potentially go wrong with it. The issue here will once again be to translate 2d images into something the SuperScanner8000 can understand and prepare against. Once again online libraries will be our biggest allies here and we will have to learn how to use them.

Page 10 | 9 RISK ASSESSMENT

10 GANTT CHART | CS-358

## 10 GANTT Chart

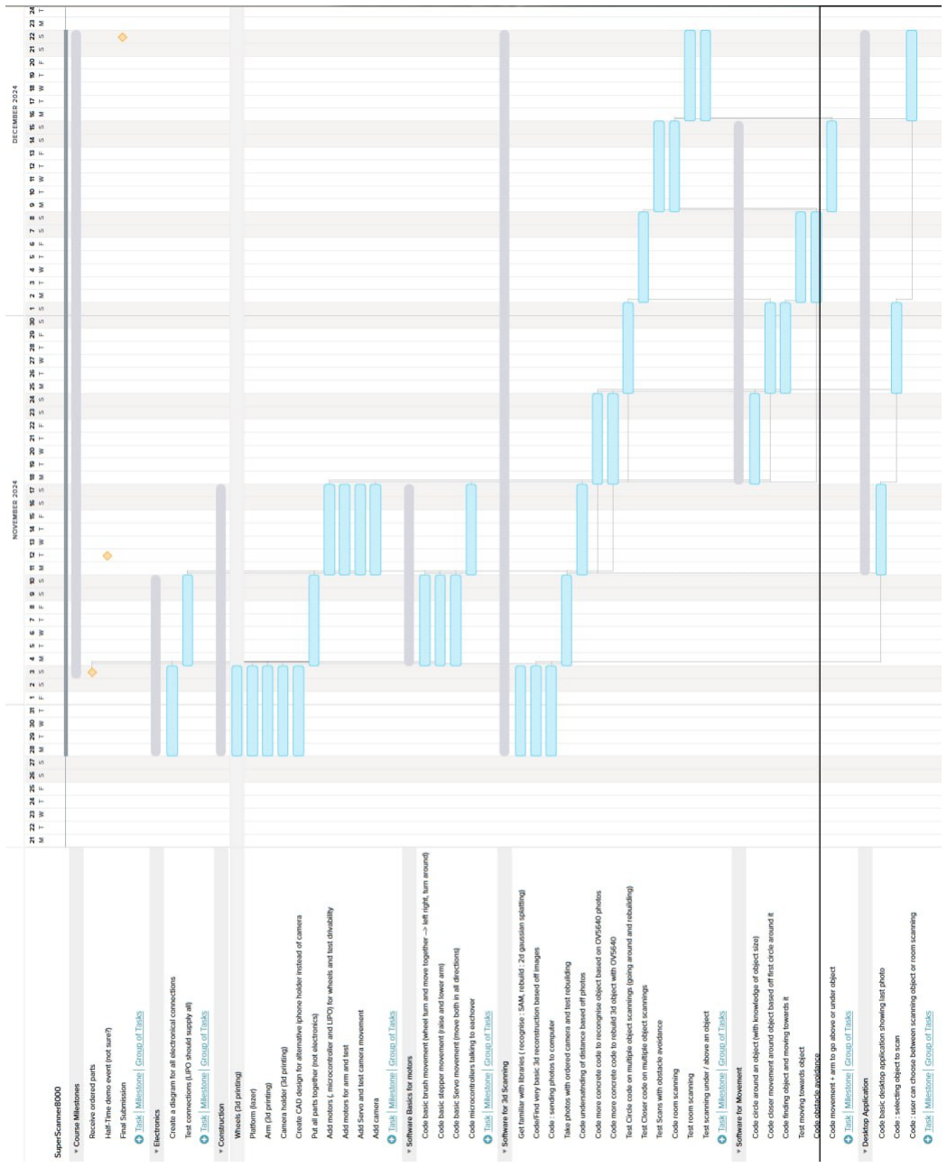
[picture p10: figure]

Figure 7: Sceenshot of GANTT Chart made on teamgantt

(Apologies for the bad quality, we couldn’t export from teamgantt without using the pay option)

Page 11 | 10 GANTT CHART

REFERENCES | CS-358

## References

[1] url: https://matterport.com/.
[2] Binbin Huang et al. “2D Gaussian Splatting for Geometrically Accurate Radiance Fields”. In: SIGGRAPH 2024 Conference Papers. Association for Computing Machinery, 2024. doi: 10.1145/3641519.3657428. (https://doi.org/10.1145/3641519.3657428)
[3] Ben Mildenhall et al. “NeRF: Representing Scenes as Neural Radiance Fields for View Synthesis”. In: ECCV. 2020. url: https://www.matthewtancik.com/nerf.
[4] pulsar123. Robotic arm for Creality CR-Scan Ferret 3d scanner. 2024. url: https://www.thingiverse.com/thing:6628782.
[5] shapespeare. “Build a DIY Desktop 3d Scanner With Infinite Resolution.” In: Instructables (2015). url: https://www.instructables.com/Build- a- DIY- Desktop- 3d- Scanner-With-Infinite-Resol/. (https://www.instructables.com/Build-a-DIY-Desktop-3d-Scanner-With-Infinite-Resol/)
Page 12 | REFERENCES

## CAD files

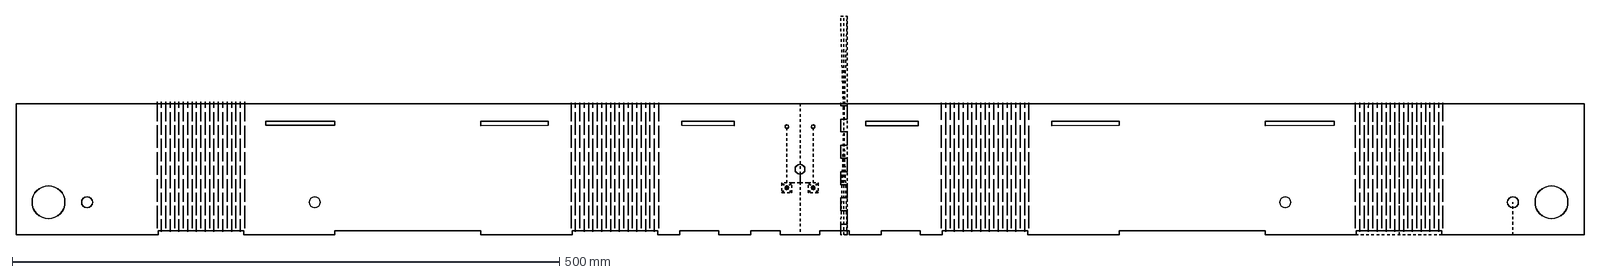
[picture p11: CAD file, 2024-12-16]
design/dxf/side_full.dxf
1432.2 x 200.0 mm

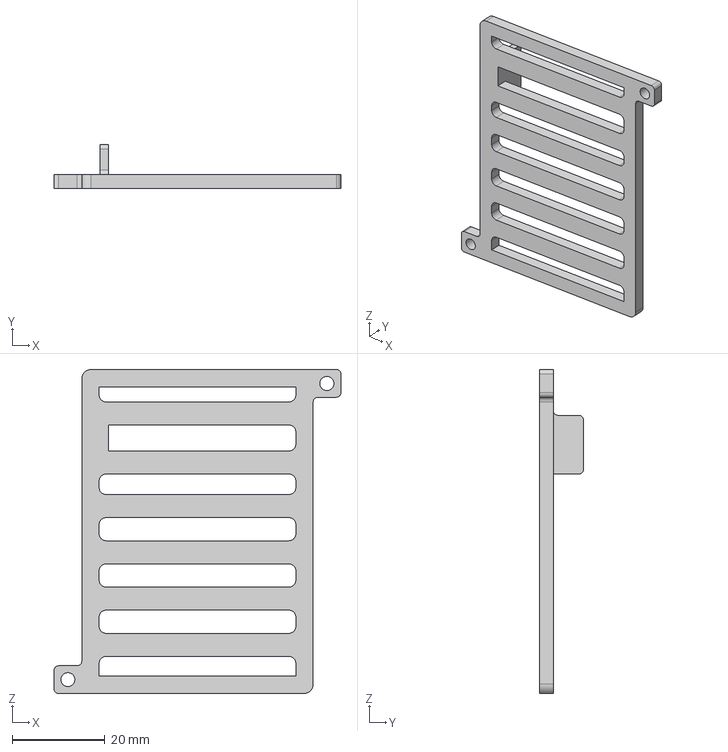
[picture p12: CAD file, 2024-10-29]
CAD/lipo_protection/step/lipo_bottom.step
62.0 x 9.50 x 70.0 mm

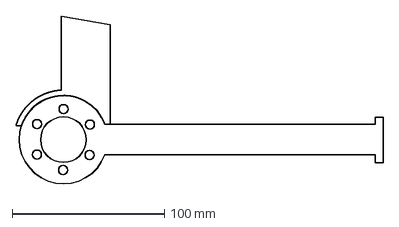
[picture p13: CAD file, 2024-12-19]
design/dxf/calibrate2.dxf
241.2 x 112.1 mm

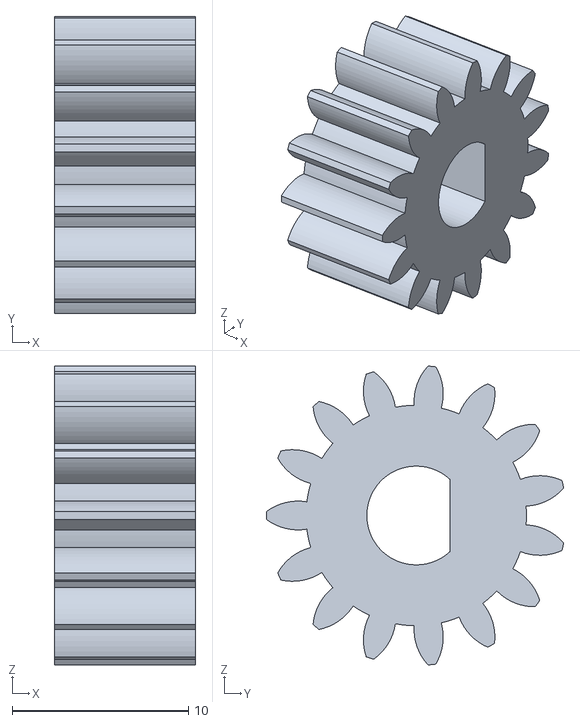
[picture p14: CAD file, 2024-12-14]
design/prints/actuators/15th_sun_stage1.stl
8.00 x 16.9 x 16.9

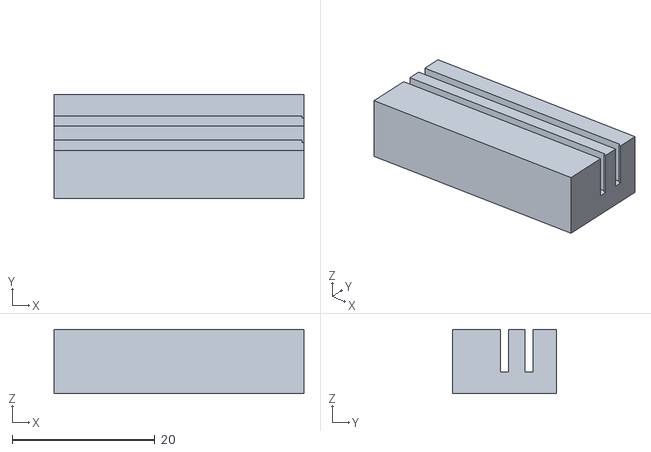
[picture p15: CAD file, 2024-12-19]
design/prints/belt_holder.stl
35.0 x 14.6 x 9.00

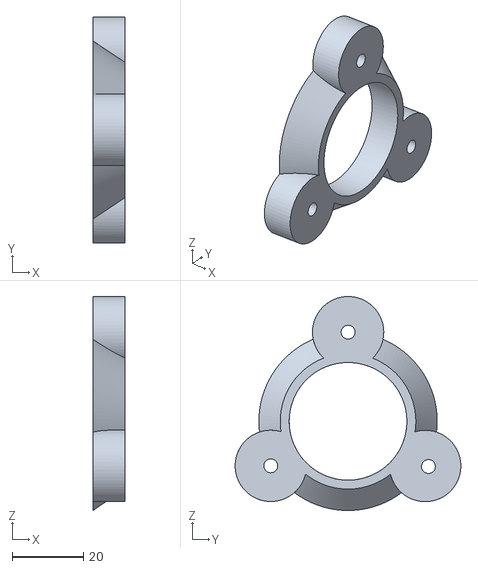
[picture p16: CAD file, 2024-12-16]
design/prints/caster/top.stl
9.00 x 63.3 x 60.0

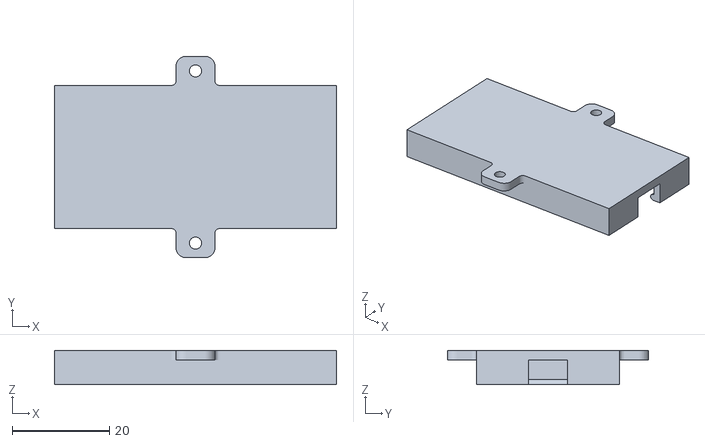
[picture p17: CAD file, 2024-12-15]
design/prints/components_supports/ESP32-S2_support.stl
58.0 x 41.4 x 7.00

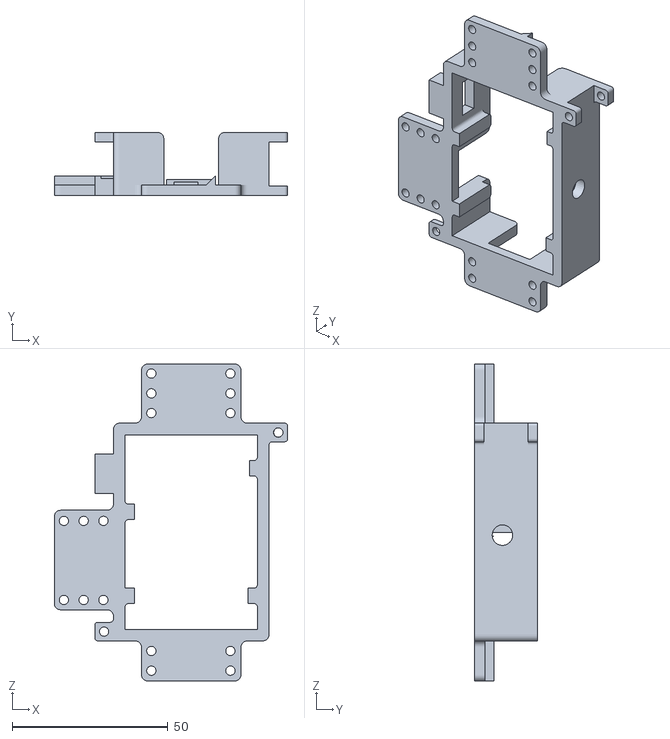
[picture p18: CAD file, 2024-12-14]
design/prints/lipo_box/lipo_box.stl
75.0 x 20.3 x 101.9

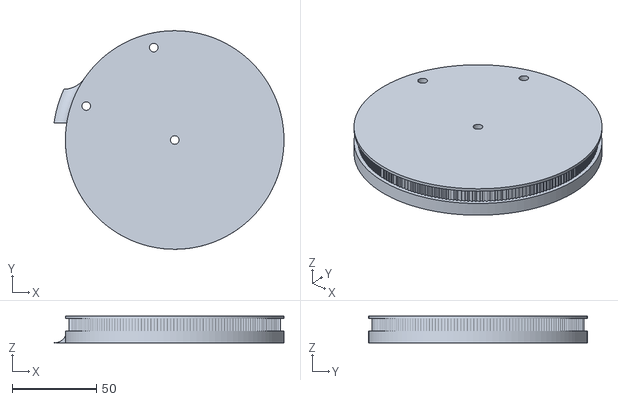
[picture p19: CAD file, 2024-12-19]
design/prints/long_arm/pulley.stl
136.8 x 130.0 x 16.0

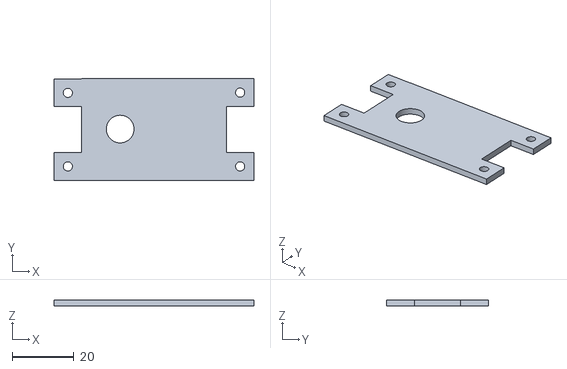
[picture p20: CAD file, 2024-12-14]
design/prints/top_axle/esp_case2.stl
65.0 x 33.0 x 2.00

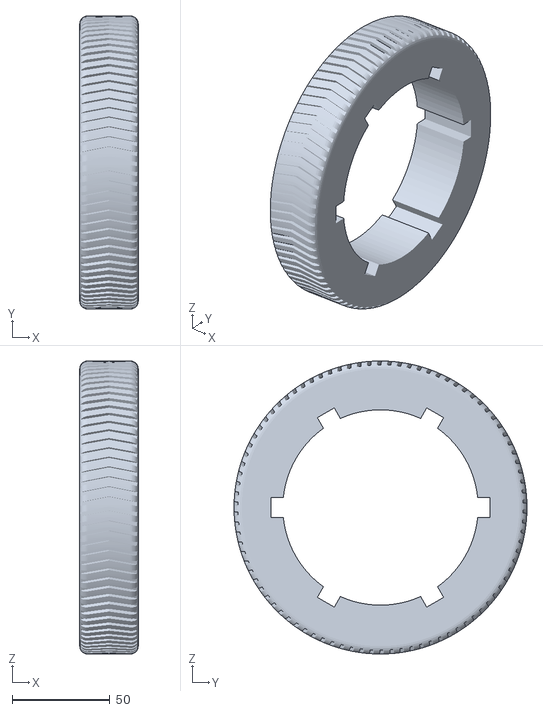
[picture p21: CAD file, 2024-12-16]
design/prints/wheels/outer_wheel.stl
30.0 x 150.0 x 150.0

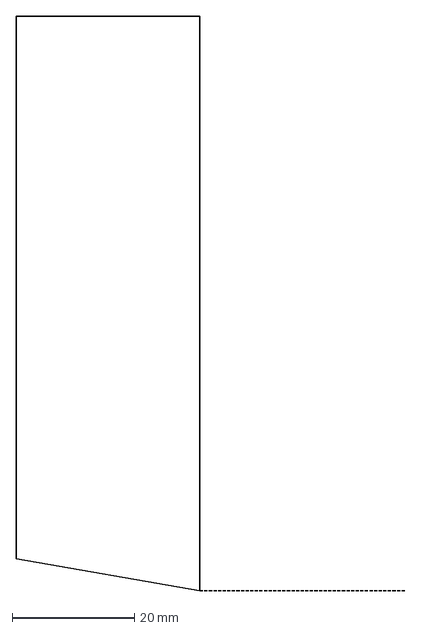
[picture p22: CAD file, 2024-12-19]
design/dxf/calibrate1.dxf
63.5 x 94.0 mm

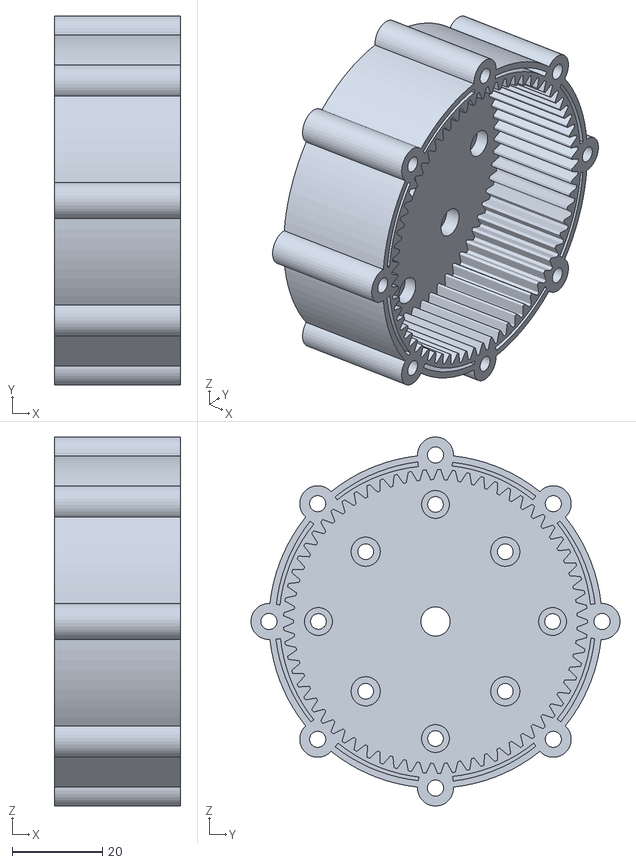
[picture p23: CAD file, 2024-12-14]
design/prints/actuators/Nema17_base_ring.stl
28.0 x 82.0 x 82.0

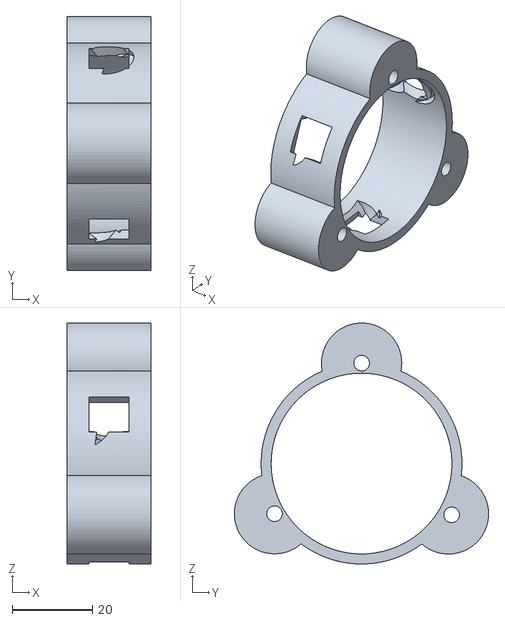
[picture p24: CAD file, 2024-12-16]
design/prints/caster/Base.stl
21.0 x 63.3 x 60.0

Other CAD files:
CAD/lipo_protection/step/lipo_box.step
design/prints/components_supports/chihai_supports.stl
design/prints/housing_on_base.stl
design/prints/lipo_box/Lipo_bottom.stl
CAD/lipo_protection/lipo_box.f3d
CAD/lipo_protection/stl/lipo_bottom.stl
CAD/lipo_protection/stl/lipo_box.stl
design/dxf/bottom_base.dxf
design/dxf/side1.dxf
design/dxf/side2.dxf
design/dxf/top_base_back.dxf
design/dxf/top_base_front.dxf
design/prints/actuators/15th_planet_carrier.stl
design/prints/actuators/25th_planet_stage1.stl
design/prints/actuators/25th_planet_stage2.stl
design/prints/actuators/Nema17_clamp.stl
design/prints/actuators/nema17_mount.stl
design/prints/caster/Body5FRWER.stl
design/prints/components_supports/CNC_shield_support.stl
design/prints/components_supports/LiPo_support.stl
design/prints/long_arm/arm1.stl
design/prints/long_arm/arm2.stl
design/prints/long_arm/arm3.stl
design/prints/long_arm/arm4.stl
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

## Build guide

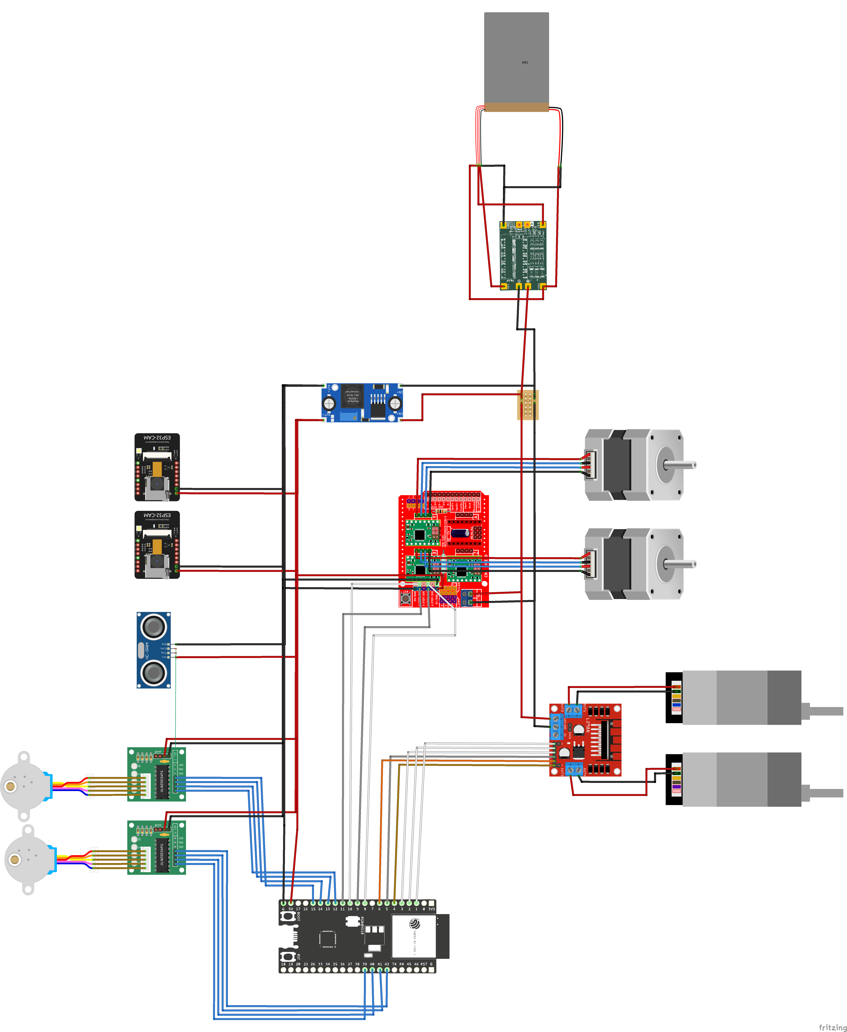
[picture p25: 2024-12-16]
Wiring Diagram/WiringDiagram.png

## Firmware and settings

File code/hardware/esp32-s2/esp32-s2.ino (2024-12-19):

#include <Arduino.h>
#include <WiFi.h>
#include <WebServer.h>
#include <LiquidCrystal.h>
#include "password.h"
#include "wheels.h"
#include "arm.h"
#include "cam_angles.h"
#include <ArduinoJson.h>
#include "display.h"
#include "led.h"

WebServer server(80);
Arm arm(21, 20, 33, 34, 7); 
Wheels wheels(2, 3, 1, 5, 4, 6);
CamAngles camera(8, 9, 10, 11, 12, 13, 14, 15, 4096);
Display display(36, 37, 38, 39, 40, 41, 35, 42); // rs, en, d4, d5, d6, d7, contrast, backlight
Led led(21);

StaticJsonDocument<250> jsonDocument; 
char buffer[250];

// set the endpoints for the API
void setup_routing() { 
  server.on("/status", get_status);   
  server.on("/fwd", HTTP_POST, fwd);     
  server.on("/bwd", HTTP_POST, bwd);
  server.on("/lft", HTTP_POST, lft);
  server.on("/rgt", HTTP_POST, rgt);
  server.on("/hrgt", HTTP_POST, hrgt);
  server.on("/hlft", HTTP_POST, hlft);
  server.on("/stp", HTTP_POST, stp);
  server.on("/speed", HTTP_POST, set_speed);

  server.on("/arm/status", arm_status);
  server.on("/arm/goto", HTTP_POST, arm_goto);
  server.on("/arm/stp", HTTP_POST, arm_stop);

  server.on("/cam/status", cam_status);
  server.on("/cam/goto", HTTP_POST, cam_goto);
  server.on("/cam/stp", HTTP_POST, cam_stop);

  server.on("/text", HTTP_POST, text);
  server.on("/progress", HTTP_POST, progress);
  server.on("/scroll", HTTP_POST, scroll);
  
  server.on("/led/set", HTTP_POST, led_set);
  server.on("/led/rainbow", HTTP_POST, led_rainbow);
  server.on("/led/flash", HTTP_POST, led_flash);
          
  server.begin();    
}

// retrieve the body of the request and parse it
void handlePost() {
  if (server.hasArg("plain") == false) {
  }
  String body = server.arg("plain");
  deserializeJson(jsonDocument, body);
}

//---- Wheels ----
// return the current direction of the wheels
void get_status() {  
  jsonDocument.clear();
  jsonDocument["direction"] = directionMap(wheels.direction);
  serializeJson(jsonDocument, buffer);
  server.send(200, "application/json", buffer);
}

void set_speed() {
  handlePost();

  int speed = jsonDocument["speed"];
  if (speed < 0 || speed > 255) {
    server.send(422, "application/json", "{}");
    return;
  }
  wheels.setDutyCycle(speed);
  server.send(200, "application/json", "{}");
}

void fwd() {
  handlePost();
  Serial.print("Forward ");
  Serial.println((int)jsonDocument["ms"]);
  wheels.forward(jsonDocument["ms"]);
  server.send(200, "application/json", "{}");
}

void bwd() {
  handlePost();
  Serial.print("Backward ");
  Serial.println((int)jsonDocument["ms"]);
  wheels.backward(jsonDocument["ms"]);
  server.send(200, "application/json", "{}");
}

void lft() {
  handlePost();
  Serial.print("Left ");
  Serial.println((int)jsonDocument["ms"]);
  wheels.left(jsonDocument["ms"]);
  server.send(200, "application/json", "{}");
}

void rgt() {
  handlePost();
  Serial.print("Right ");
  Serial.println((int)jsonDocument["ms"]);
  wheels.right(jsonDocument["ms"]);
  server.send(200, "application/json", "{}");
}

void hrgt() {
  handlePost();
  Serial.print("Hard right ");
  Serial.println((int)jsonDocument["ms"]);
  wheels.hard_right(jsonDocument["ms"]);
  server.send(200, "application/json", "{}");
}

void hlft() {
  handlePost();
  Serial.print("Hard left ");
  Serial.println((int)jsonDocument["ms"]);
  wheels.hard_left(jsonDocument["ms"]);
  server.send(200, "application/json", "{}");
}

void stp() {
  Serial.println("Stop");
  wheels.stop();
  server.send(200, "application/json", "{}");
}

//---- Arm ----
// return the current position of the arm and if it is currently moving
void arm_status() {
  jsonDocument.clear();
  jsonDocument["x"] = arm.x;
  jsonDocument["y"] = arm.y;
  jsonDocument["q1"] = arm.q1;
  jsonDocument["q2"] = arm.q2;
  jsonDocument["moving"] = arm.getMoving();
  serializeJson(jsonDocument, buffer);
  server.send(200, "application/json", buffer);
}

void arm_goto() {
  handlePost();

  Serial.println("Arm goto");
  int x = jsonDocument["x"];
  int y = jsonDocument["y"];

  bool angles = false;
  if (jsonDocument.containsKey("angles")) {
    angles = jsonDocument["angles"];
  }
  Serial.println(x);
  Serial.println(y);
  Serial.println(angles);

  if (arm.setPos(x, y, angles) == -1) {
    server.send(422, "application/json", "{}");
    return;
  }

  jsonDocument.clear();
  jsonDocument["x"] = arm.x;
  jsonDocument["y"] = arm.y;
  jsonDocument["q1"] = arm.q1 / PI * 180;
  jsonDocument["q2"] = arm.q2 / PI * 180;
  serializeJson(jsonDocument, buffer);
  server.send(200, "application/json", buffer);
}

void arm_stop() {
  Serial.println("Arm stop");
  arm.stop();
  server.send(200, "application/json", "{}");
}


//---- Camera ----
void cam_status() {
  jsonDocument.clear();
  jsonDocument["moving"] = camera.isMoving();
  jsonDocument["alpha"] = camera.stepsToAngle(1);
  jsonDocument["beta"] = camera.stepsToAngle(2);
  serializeJson(jsonDocument, buffer);
  server.send(200, "application/json", buffer);
}

void cam_goto() {
  handlePost();

  float angle1 = jsonDocument["alpha"];
  float angle2 = jsonDocument["beta"];

  if (camera.moveToAngles(angle1, angle2) == -1){
    server.send(422, "application/json", "{}");
    return;
  }

  jsonDocument.clear();
  jsonDocument["angle1"] = angle1;
  jsonDocument["angle2"] = angle2;
  serializeJson(jsonDocument, buffer);

  server.send(200, "application/json", buffer);
}

void cam_stop() {
  handlePost();
  Serial.println("cam stop");
  camera.stop();

  jsonDocument.clear();
  jsonDocument["alpha"] = camera.stepsToAngle(1);
  jsonDocument["beta"] = camera.stepsToAngle(2);
  serializeJson(jsonDocument, buffer);

  server.send(200, "application/json", buffer);
}

//---- Display ----
void text() {
  handlePost();
  
  String text = jsonDocument["text"];
  
  display.print(text);

  Serial.print("Text is: ");
  Serial.println(text);

  server.send(200, "application/json", "{}");
}

void progress() {
  handlePost();
  
  String text = jsonDocument["text"];
  int progress = jsonDocument["progress"];
  
  if(progress < 0 || progress > 100 || text.length() > 16) {
    server.send(422, "application/json", "{}");
    return;
  }
  display.printProgressBar(text, progress);

  Serial.print("Text is: ");
  Serial.println(text);
  Serial.print("Progress is: ");
  Serial.println(progress);

  server.send(200, "application/json", "{}");
}

void scroll() {
  handlePost();
  
  String text1 = jsonDocument["text1"];
  String text2 = jsonDocument["text2"];
  
  display.scroll(text1, text2);

  server.send(200, "application/json", "{}");
}

//---- Led ----
void led_set() {
  handlePost();
  
  int r = jsonDocument["r"];
  int g = jsonDocument["g"];
  int b = jsonDocument["b"];
  
  led.setAll(r, g, b);
  led.show();

  Serial.println("leds set");

  server.send(200, "application/json", "{}");
}

void led_rainbow() {
  handlePost();
  
  led.rainbowMode = (bool) jsonDocument["rainbow"];
  Serial.println(led.rainbowMode);
  Serial.println("rainbow leds");

  server.send(200, "application/json", "{}");
}

void led_flash() {
  handlePost();
  
  int r = jsonDocument["r"];
  int g = jsonDocument["g"];
  int b = jsonDocument["b"];
  int duration = jsonDocument["duration"];
  
  led.flash(r, g, b, duration);

  Serial.println("leds flash");

  server.send(200, "application/json", "{}");
}


void setup() {
  Serial.begin(115200); 

  arm.setup();
  wheels.setup();
  camera.setup();
  display.setup();
  led.setup();

  led.setAll(255, 0, 0);
  led.show();
  display.scroll("Connecting to Wi-Fi", "Please wait"); 

  Serial.print("Connecting to Wi-Fi with password ");
  Serial.println(PWD);
  // access the esp by http://superscanner8000/ when connected to the same network
  WiFi.setHostname("superscanner8000");
  WiFi.begin(SSID, PWD);
  while (WiFi.status() != WL_CONNECTED) {
    Serial.print(".");
    delay(500);
  }
  
  display.scroll("Connected to Wi-Fi with hostname superscanner8000", "");
  led.setAll(255, 10, 0);
  led.show();
  Serial.print("Connected! IP Address: ");
  Serial.println(WiFi.localIP()); 
  setup_routing();
}
       
void loop() {    
  server.handleClient();     
  arm.update();
  wheels.update();
  camera.update();
  display.update();
  led.update();
}

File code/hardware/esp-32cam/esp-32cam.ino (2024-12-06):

#include "esp_camera.h"
#include <WiFi.h>
#include <WebServer.h>
#include <WiFiClient.h>
#include <ESPmDNS.h>


// Camera configuration for the AI Thinker model
#define PWDN_GPIO_NUM     32
#define RESET_GPIO_NUM    -1
#define XCLK_GPIO_NUM      0
#define SIOD_GPIO_NUM     26
#define SIOC_GPIO_NUM     27

#define Y9_GPIO_NUM       35
#define Y8_GPIO_NUM       34
#define Y7_GPIO_NUM       39
#define Y6_GPIO_NUM       36
#define Y5_GPIO_NUM       21
#define Y4_GPIO_NUM       19
#define Y3_GPIO_NUM       18
#define Y2_GPIO_NUM        5
#define VSYNC_GPIO_NUM    25
#define HREF_GPIO_NUM     23
#define PCLK_GPIO_NUM     22

// Wi-Fi credentials
const char* ssid = "SPOT-iot";
const char* password = "SuccionPourquoiSensation5900";
String computerIP ="";
WiFiUDP udp; 

WiFiServer server(12346);  // TCP server to listen for incoming connection



void startCamera() {
  camera_config_t config;
  config.ledc_channel = LEDC_CHANNEL_0;
  config.ledc_timer = LEDC_TIMER_0;
  config.pin_d0 = Y2_GPIO_NUM;
  config.pin_d1 = Y3_GPIO_NUM;
  config.pin_d2 = Y4_GPIO_NUM;
  config.pin_d3 = Y5_GPIO_NUM;
  config.pin_d4 = Y6_GPIO_NUM;
  config.pin_d5 = Y7_GPIO_NUM;
  config.pin_d6 = Y8_GPIO_NUM;
  config.pin_d7 = Y9_GPIO_NUM;
  config.pin_xclk = XCLK_GPIO_NUM;
  config.pin_pclk = PCLK_GPIO_NUM;
  config.pin_vsync = VSYNC_GPIO_NUM;
  config.pin_href = HREF_GPIO_NUM;
  config.pin_sccb_sda = SIOD_GPIO_NUM;
  config.pin_sccb_scl = SIOC_GPIO_NUM;
  config.pin_pwdn = PWDN_GPIO_NUM;
  config.pin_reset = RESET_GPIO_NUM;
  config.xclk_freq_hz = 20000000;
  config.pixel_format = PIXFORMAT_JPEG;

  config.frame_size = FRAMESIZE_QVGA; // Adjust the frame size here
  config.jpeg_quality = 12; // 0-63 lower means higher quality
  config.fb_count = 1;

  // Camera init
  esp_err_t err = esp_camera_init(&config);
  if (err != ESP_OK) {
    Serial.printf("Camera init failed with error 0x%x", err);
    return;
  }
}


void setup() {
  Serial.begin(115200);

  WiFi.setHostname("superscanner8008");


  WiFi.begin(ssid, password);
  while (WiFi.status() != WL_CONNECTED) {
    delay(500);
    Serial.print(".");
  }
  Serial.println("WiFi connected");
  Serial.print("IP address: ");
  Serial.println(WiFi.localIP());
  if (!MDNS.begin("superscanner8008")) {
  Serial.println("Error starting mDNS");
} else {
  Serial.println("mDNS responder started");
}

// Wait for the connection and receive the computer's IP address
 
  server.begin();


  // Initialize the camera
  startCamera();

  udp.begin(12345);
}

void loop() {
   // Check for incoming TCP connection to get the computer's IP address
  WiFiClient client = server.available();
  if (client) {
    Serial.println("Client connected");
    String ipMessage = "";
    while (client.connected()) {
      if (client.available()) {
        ipMessage = client.readStringUntil('\n');
        if (ipMessage.startsWith("IP:")) {
          computerIP = ipMessage.substring(3);  // Extract the IP address
          Serial.println("Received IP address: " + computerIP);
          client.stop();  // Close TCP connection after receiving the IP
          break;
        }
      }
    }
  }



    if (computerIP != "") {
      // Capture an image from the camera
      camera_fb_t *fb = esp_camera_fb_get();
      if (!fb) {
        Serial.println("Failed to capture image");
        return;
      }// Send the captured image over UDP to the computer IP
      udp.beginPacket(computerIP.c_str(), 12346);  // Use the computer's IP address and port for UDP
      udp.write(fb->buf, fb->len);  // Send the frame data
      udp.endPacket();

      Serial.println("Image sent via UDP");

      esp_camera_fb_return(fb);  // Free memory

      delay(300);  
    }
}

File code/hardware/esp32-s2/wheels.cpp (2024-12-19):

#include "esp32-hal.h"
#include "wheels.h"
#include <Arduino.h>

const float WHEEL_DIAMETER_CM = 15.0; // Diameter of the wheel in cm
const float WHEEL_CIRCUMFERENCE_CM = 3.1416 * WHEEL_DIAMETER_CM; // Circumference of the wheel in cm
const int MAX_RPM = 110; // Max RPM of the motor
const float TRACK_WIDTH_CM = 26.0; // Distance between the two wheels in cm
const float CM_PER_SECOND = 15.0; // Distance per second in cm
const float SECONDS_PER_TURN = 10; // Time in seconds to turn 360 degrees
const float ANGLE_PER_SECOND = 360 / SECONDS_PER_TURN; // Angle per second in degrees

char* directionMap(Direction Direction) {
    switch (Direction) {
        case FORWARD:
            return "forward";
        case BACKWARD:
            return "backward";
        case LEFT:
            return "left";
        case RIGHT:
            return "right";
        case HARD_LEFT:
            return "hard left";
        case HARD_RIGHT:
            return "hard right";
        case STOP:
            return "stop";
        default:
            return "unknown";
    }
}

Wheels::Wheels(int m1Pin1, int m1Pin2, int m1En, int m2Pin1, int m2Pin2, int m2En)
    :   motor1Pin1(m1Pin1), 
        motor1Pin2(m1Pin2),
        enable1Pin(m1En),

        motor2Pin1(m2Pin1),
        motor2Pin2(m2Pin2),
        enable2Pin(m2En),

        freq(30000),
        resolution(8),
        pwmChannel1(0),
        pwmChannel2(1),

        dutyCycle(255),
        distancePerSecond(0.0),

        t(0),
        targetTime(0),
        direction(STOP) {

}

void Wheels::setup() {
    // sets the pins as outputs:
    pinMode(motor1Pin1, OUTPUT);
    pinMode(motor1Pin2, OUTPUT);
    pinMode(enable1Pin, OUTPUT);

    pinMode(motor2Pin1, OUTPUT);
    pinMode(motor2Pin2, OUTPUT);
    pinMode(enable2Pin, OUTPUT);
    
    analogWrite(enable1Pin, dutyCycle);
    analogWriteResolution(enable1Pin, 8);
    analogWriteFrequency(enable1Pin, 30000);
    analogWrite(enable2Pin, dutyCycle);
    analogWriteResolution(enable2Pin, 8);
    analogWriteFrequency(enable2Pin, 30000);

    updateDistancePerSecond();
}

void Wheels::updateDistancePerSecond() {
    float currentRPM = MAX_RPM * (dutyCycle / 100.0); // RPM at given duty cycle
    float rps = currentRPM / 60.0;                    // Rotations per second
    distancePerSecond = WHEEL_CIRCUMFERENCE_CM * rps; // Distance per second in cm
}

void Wheels::setDutyCycle(int newDutyCycle) {
    dutyCycle = newDutyCycle;

    // Update PWM output
    analogWrite(enable1Pin, freq);
    analogWrite(enable2Pin, resolution);

    // Update cached distance per second
    updateDistancePerSecond();
}

// updates the wheels. If the target time is set, it will stop the wheels after the target time is reached
void Wheels::update() {
    if (targetTime > 0 && millis() - t > targetTime) {
        Serial.println("wheels:: time is up");
        stop();
        direction = STOP;
    }
}

// stop the wheels
void Wheels::stop() {
    targetTime = 0;
    direction = STOP;
    digitalWrite(motor1Pin1, LOW);
    digitalWrite(motor1Pin2, LOW);
    digitalWrite(motor2Pin1, LOW);
    digitalWrite(motor2Pin2, LOW);
}

/** move the wheels forward for ms milliseconds. Moves indefinitely if ms is smaller than 0
 * @param ms the time in milliseconds to move, smaller than 0 to move indefinitely
 */
void Wheels::forward(int ms) {
    Wheels::stop();
    t = millis();
    targetTime = ms; 
    direction = FORWARD;
    digitalWrite(motor1Pin1, HIGH);
    digitalWrite(motor1Pin2, LOW);
    digitalWrite(motor2Pin1, HIGH);
    digitalWrite(motor2Pin2, LOW);
}

/** move the wheels backward for ms milliseconds. Moves indefinitely if ms is smaller than 0
 * @param ms the time in milliseconds to move, smaller than 0 to move indefinitely
 */
void Wheels::backward(int ms) {
    Wheels::stop();
    t = millis();
    targetTime = ms;
    direction = BACKWARD;
    digitalWrite(motor1Pin1, LOW);
    digitalWrite(motor1Pin2, HIGH);
    digitalWrite(motor2Pin1, LOW);
    digitalWrite(motor2Pin2, HIGH);
}

/** turn one wheel left for ms milliseconds. Moves indefinitely if ms is smaller than 0
 * @param ms the time in milliseconds to turn, smaller than 0 to move indefinitely
 */
void Wheels::left(int ms) {
    Wheels::stop();
    t = millis();
    targetTime = ms;
    direction = LEFT;
    digitalWrite(motor1Pin1, HIGH);
    digitalWrite(motor1Pin2, LOW);
}

/** turn one wheel right for ms milliseconds. Moves indefinitely if ms is smaller than 0
 * @param ms the time in milliseconds to turn, smaller than 0 to move indefinitely
 */
void Wheels::right(int ms) {
    Wheels::stop();
    t = millis();
    targetTime = ms;
    direction = RIGHT;
    digitalWrite(motor1Pin1, LOW);
    digitalWrite(motor1Pin2, HIGH);
}

/** turn both wheels left (turn on itself) for ms milliseconds. Moves indefinitely if ms is smaller than 0
 * @param ms the time in milliseconds to turn, smaller than 0 to move indefinitely
 */
void Wheels::hard_left(int ms) {
    Wheels::stop();
    t = millis();
    targetTime = ms;
    direction = HARD_LEFT;
    digitalWrite(motor1Pin1, HIGH);
    digitalWrite(motor1Pin2, LOW);
    digitalWrite(motor2Pin1, LOW);
    digitalWrite(motor2Pin2, HIGH);
}

/** turn both wheels right (turn on itself) for ms milliseconds. Moves indefinitely if ms is smaller than 0
 * @param ms the time in milliseconds to turn, smaller than 0 to move indefinitely
 */
void Wheels::hard_right(int ms) {
    Wheels::stop();
    t = millis();
    targetTime = ms;
    direction = HARD_RIGHT;
    digitalWrite(motor1Pin1, LOW);
    digitalWrite(motor1Pin2, HIGH);
    digitalWrite(motor2Pin1, HIGH);
    digitalWrite(motor2Pin2, LOW);
}

// Function with cm distance

/** move the wheels forward for cm centimeters
 * @param cm the distance in centimeters to move
 */
void Wheels::forward_cm(int cm) {
    int ms = (cm / CM_PER_SECOND) * 1000; 
    forward(ms);
}

/** move the wheels backward for cm centimeters
 * @param cm the distance in centimeters to move
 */
void Wheels::backward_cm(int cm) {
    int ms = (cm / CM_PER_SECOND) * 1000;
    backward(ms);
}

/** turn left on itself for angle degrees
 * @param angle the angle in degrees to turn
 */
void Wheels::hard_left_angle(float angle) {
    // float angularVelocity = (distancePerSecond * 360) / (3.1416 * TRACK_WIDTH_CM);
    float timeInSeconds = angle / ANGLE_PER_SECOND;
    int ms = timeInSeconds * 1000;

    hard_left(ms);
}

/** turn right on itself for angle degrees
 * @param angle the angle in degrees to turn
 */
void Wheels::hard_right_angle(float angle) {
    // float angularVelocity = (distancePerSecond * 360) / (3.1416 * TRACK_WIDTH_CM);
    float timeInSeconds = angle / ANGLE_PER_SECOND;
    int ms = timeInSeconds * 1000;

    hard_right(ms);
}

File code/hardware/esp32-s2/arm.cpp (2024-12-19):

#include "HardwareSerial.h"
#include "arm.h"
#include <AccelStepper.h>
#include <Arduino.h>

#define INIT_ANGLE 5. / 180. * PI
#define DEG_TO_RAD PI / 180.

Arm::Arm(int m1Step, int m1Dir, int m2Step, int m2Dir, int _enablePin):   
    enablePin(_enablePin), 
    stepper1(AccelStepper::DRIVER, m1Step, m1Dir), 
    stepper2(AccelStepper::DRIVER, m2Step, m2Dir), 
    x(0), 
    y(0), 
    a1(40), 
    a2(40),
    gearFactor(30), // 28
    pulleyFactor(200. / 20.),
    fullRevolution(200), 
    q1(0), 
    q2(0) 
    {}

// Setup function for the arm. Initializes the steppers and sets the enable pin
void Arm::setup() {
    pinMode(enablePin, OUTPUT);
    digitalWrite(enablePin, LOW);

    stepper1.setMaxSpeed(1000.0);
    stepper1.setAcceleration(100.0);

    stepper2.setMaxSpeed(1000.0);
    stepper2.setAcceleration(100.0);
}

int Arm::setPos(int _x, int _y) {
    return setPos(_x, _y, false);
}

/** Set the position of the arm in either angles or coordinates
 * @param _x the x coordinate or angle in degrees
 * @param _y the y coordinate or angle in degrees
 * @param angles true if the input is in angles, false if it is in coordinates
 */
int Arm::setPos(int _x, int _y, bool angles) {
    if (angles){
        if (_x < -8 || _x > 190 || _y < 0 || _y > 190) {
            Serial.println("Error: Angles out of range.");
            return -1;
        }
        // q1 and q2 are in radians
        q1 = _x * DEG_TO_RAD;
        q2 = _y * DEG_TO_RAD;
        angleToPos();
    } else {
        if (sqrt(pow(x, 2) + pow(y, 2)) > (a1 + a2) || sqrt(pow(x, 2) + pow(y, 2)) < abs(a1 - a2)) {
            Serial.println("Error: Coordinates out of range.");
            return -1;
        }
        long oldX = x;
        long oldY = y;
        x = _x;
        y = _y;
        if (posToAngles() < 0) {
            x = oldX;
            y = oldY;
            return -1;
        }
    }

    // Move the steppers
    stepper1.moveTo(gearFactor * fullRevolution * (q1 - INIT_ANGLE) / (2 * PI));
    stepper2.moveTo(pulleyFactor * fullRevolution * (q2 - INIT_ANGLE) / (2 * PI));

    Serial.println("Moving to : " + String(fullRevolution * q1 / (2 * PI)) + ", " + String(fullRevolution * q2 / (2 * PI)));
    return 0;
}

// Stop the arm
void Arm::stop() {
    float accel = stepper1.acceleration();
    stepper1.setAcceleration(10000);
    stepper2.setAcceleration(10000);
    stepper1.moveTo(stepper1.currentPosition());
    stepper2.moveTo(stepper2.currentPosition());
    q1 = stepper1.currentPosition() * 2 * PI / (gearFactor * fullRevolution);
    q2 = stepper2.currentPosition() * 2 * PI / (pulleyFactor * fullRevolution);
    angleToPos();
    stepper1.setAcceleration(accel);
    stepper2.setAcceleration(accel);
}

// Check if the arm is moving
bool Arm::getMoving() {
    return stepper1.distanceToGo() != 0 || stepper2.distanceToGo() != 0;
}

// Update function to move the arm
void Arm::update() {
    if (stepper1.distanceToGo() != 0) {
        stepper1.run();
    }
    if (stepper2.distanceToGo() != 0) {
        stepper2.run();
    }
}

// Convert position to angles
int Arm::posToAngles() {
    float _q2 = acos((pow(x, 2) + pow(y, 2) - pow(a1, 2) - pow(a2, 2)) / (2 * a1 * a2)); 
    if (_q2 < 0) {
        _q2 = -_q2;
    } else if (q2 > PI) {
        _q2 = 2 * PI - _q2;
    }
    // float _q1 = atan2(y, x) - atan2(a2 * sin(_q2), (a1 + a2 * cos(_q2)));
    float _q1 = atan2(y, x) - acos((pow(a1, 2) + pow(x, 2) + pow(y, 2) - pow(a2, 2)) / (2 * a1 * sqrt(pow(x, 2) + pow(y, 2))));
    if (_q1 < 0) {
        _q1 = 2 * PI + _q1;
    }
    if (_q1 < -8. * DEG_TO_RAD || _q1 > 190. * DEG_TO_RAD || _q2 < 0. || _q2 > 190. * DEG_TO_RAD) {
        Serial.print("Error: Angles out of range. Angles are q1=");
        Serial.print(_q1 / PI * 180.);
        Serial.print(", q2=");
        Serial.println(180 - _q2 / PI * 180.);
        return -1;
    }
    q1 = _q1;
    q2 = 180 * DEG_TO_RAD - _q2;
    return 0;
}

// Convert angles to position
void Arm::angleToPos() {
    x = a1 * cos(q1) + a2 * cos(q1 + q2);
    y = a1 * sin(q1) + a2 * sin(q1 + q2);
}

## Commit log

2024-10-19 Completed BOM
2024-10-20 added few parts to BOM
2024-10-20 add images of CAD
2024-10-29 add lipo_protection
    [lipo_bottom.step, lipo_bottom.stl, lipo_box.f3d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]
2024-11-04 Added electronic plan
    [WiringDiagram.fzz]
2024-11-06 updated with Chihai
    [WiringDiagram.fzz]
2024-11-13 updated diagram
    [WiringDiagram.fzz]
2024-11-19 added steppers and cnc shield
    [WiringDiagram.fzz]
2024-11-20 Implemented realtime image segmentation on esp32-cam feed
2024-11-21 changed NEMA wiring + switched steppers alim from 12v to 5v
    [WiringDiagram.fzz]
2024-11-26 Create esp-32cam.ino
    Sending UDP frames
2024-11-27 interface with esp32s2
2024-11-28 moved arm and wheels algo with rest api
2024-11-29 fixed a few mistakes
    [rest_api.ino]
2024-11-30 updated wiring according to code
    [WiringDiagram.fzz]
2024-12-01 add setup button
2024-12-02 one wheel was backward
    [WiringDiagram.fzz]
2024-12-03 create camera angle functions and compensator for camera when arm moving
2024-12-03 Update esp-32cam.ino
    Camera initialzation
2024-12-03 fixed arm control
2024-12-03 add setup buttons
2024-12-06 Update esp-32cam.ino
    Camera fonctionne
2024-12-10 Added endpoints for camera
2024-12-11 upd working with thread
2024-12-11 improved arm + added limits
2024-12-13 revert to original functions
    [esp32-s2.ino]
2024-12-14 Added Side mdf cut
    4mm mdf cutting side
    [Side1.dxf, Side2.dxf]
2024-12-14 Added top,bottom and full side dxf cut
    if you got long laser cutting machine I added full side dxf cut if needed
    [Bottom base.dxf, Side full.dxf, Top base back.dxf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]
2024-12-14 Create printable directories
2024-12-14 Add files of the big arm
    ^^
    [Arm 1st part.stl, Arm 2nd part.stl, Arm 3rd part.stl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]
2024-12-15 Add electronics supports
    [CNC shield support.stl, Chihai supports.stl, ESP32-S2 support.stl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]
2024-12-15 added coments and fixed inconsistencies
    [arm.cpp, esp32-s2.ino, wheels.cpp]
2024-12-15 added design folder
    [15th Planet Carrier.stl, 15th Sun Stage1.stl, 25th Planet Stage 1.stl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]
2024-12-15 camelcase file names
    [15th_planet_carrier.stl, 15th_sun_stage1.stl, 25th_planet_stage1.stl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]
2024-12-16 threaded udp receiver
2024-12-16 updated pins according to code
    [WiringDiagram.fzz]
2024-12-16 fixed wheels not moving
    [esp32-s2.ino, wheels.cpp]
2024-12-16 added wheel design
    [inner_wheel.stl, outer_wheel.stl]
2024-12-16 udp receiver can save frame
2024-12-16 fixed empty frame issue
2024-12-17 fixed display + arm
    [arm.cpp, esp32-s2.ino]
2024-12-17 integrate arm positions into software
2024-12-17 fixed UI threading issue
2024-12-17 implement moving arm (not working)
2024-12-17 fix setupo mov buttons
2024-12-18 update cam movements + add reverse kinematics (not working)
2024-12-18 fix segmenter bug with threading
2024-12-18 remove useless print
2024-12-19 add buttons for track with body angle
2024-12-19 added leds, fixed arm, fixed cam
    [arm.cpp, cam_angles.cpp, esp32-s2.ino]
2024-12-19 added display prints with leds
2024-12-19 Update and rename Calibrate 2.dxf to calibrate2.dxf
    [calibrate2.dxf]
2024-12-19 Update and rename Calibrate1.dxf to calibrate1.dxf
    [calibrate1.dxf]
2024-12-19 added led flash duration
2024-12-19 added arm stls
    [arm3.stl, pulley.stl]
2024-12-19 added belt holder
    [belt_holder.stl]
2024-12-19 added flash leds
2024-12-19 Rename output file to remove 'frame_' prefix in UDPReceiver
2024-12-19 Enhance Navigator class to save frame and mask on reaching the last point
2024-12-19 adapted positions based on arm capbilities
2024-12-19 Fix bugs before demo #ugo apprend ä coder du soft yavait des ewrreurs partout
2024-12-20 update arm coords
2024-12-20 refactor object detection logic and update ground mask handling
2024-12-20 add sleeping time before moving between reach points + custom positions for less than 3 arm pos
